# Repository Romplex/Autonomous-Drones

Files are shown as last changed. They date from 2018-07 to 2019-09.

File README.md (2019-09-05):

# Autonomous-Drones
## Pinout:
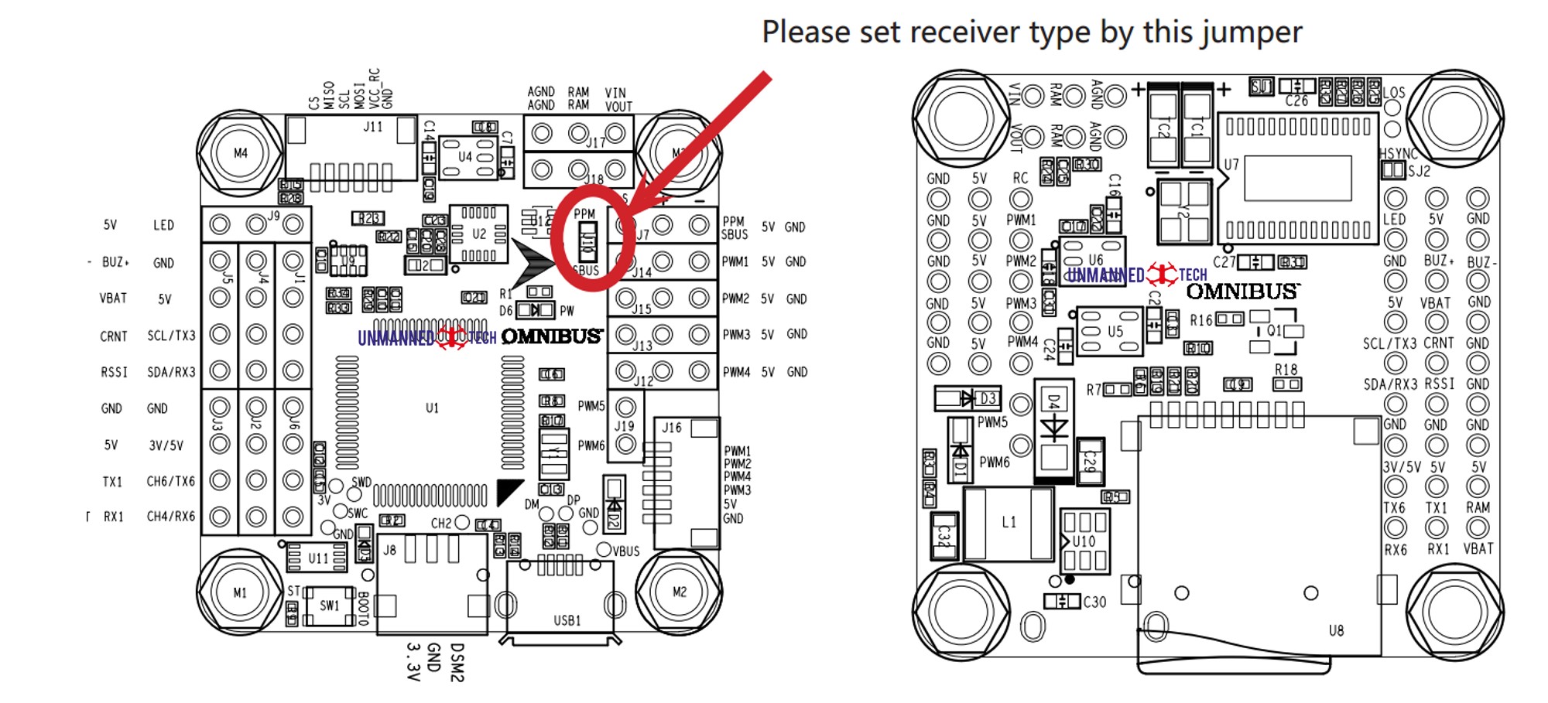
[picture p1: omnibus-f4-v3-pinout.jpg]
Omnibus Pinout


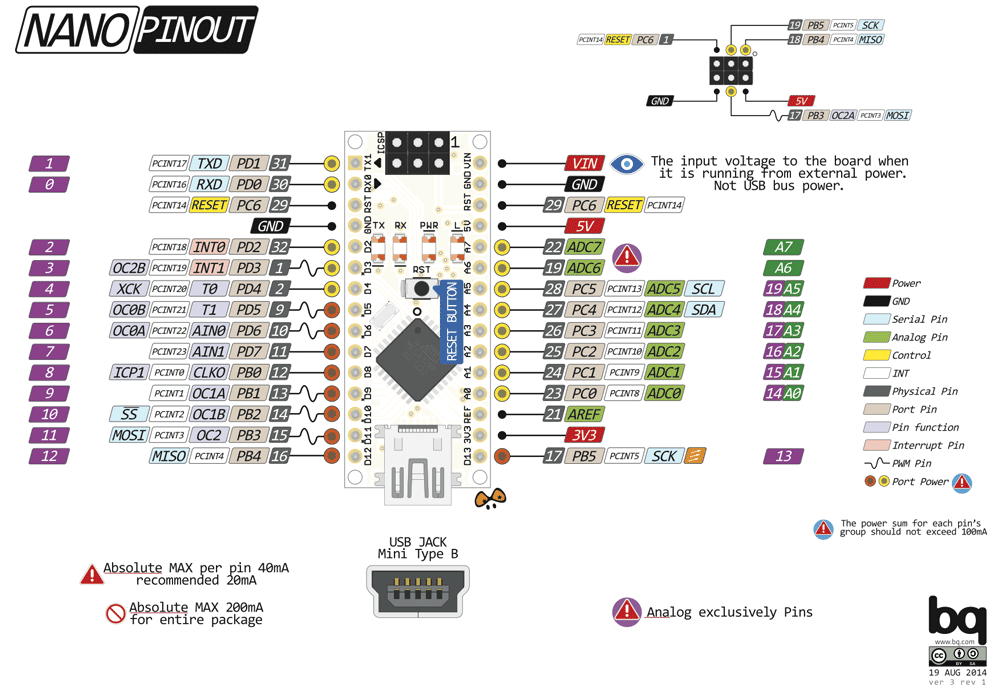
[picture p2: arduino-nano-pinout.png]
Arduino Nano Pinout


Pozyx Pinout

## Inav Settings:
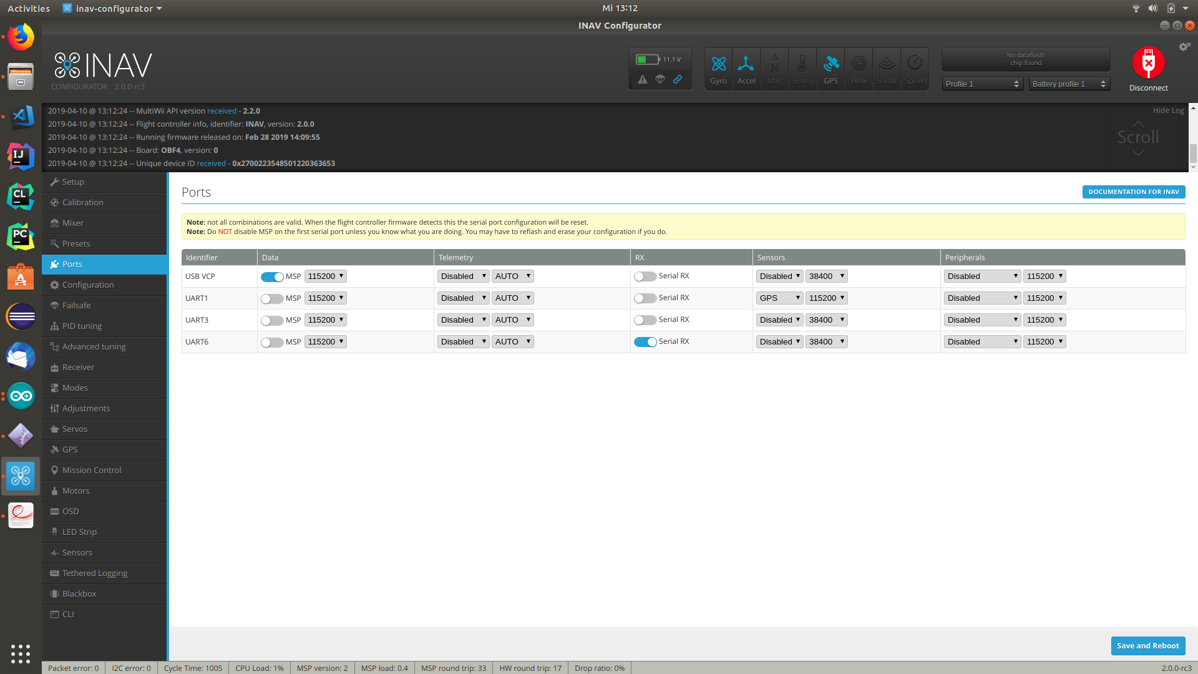
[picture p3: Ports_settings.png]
Inav Configurator Ports Inav ports


## Architektur für Kommunikation:
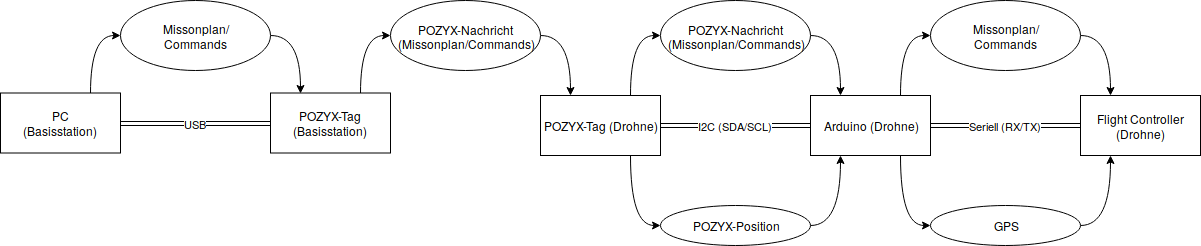
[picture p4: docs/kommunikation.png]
Logo Title Text 1


## LiPos Laden:
* Ladestärke 5A 
* 11.1V 
* LiPo (3S für 3 Zellen) 
* "Start" gedrükt halten bis es piept
* "Enter" zur Bestätigung der Einstellungen drücken

## POZYX Channel Settings
ultra-wideband channel 5, preamble length 1024, prf 64MHz, and bitrate 110kbps

## POZYX Anchor-IDs:
* 0x6951 - 1500mm
* 0x6e59 - 2000mm
* 0x695d - 2500mm
* 0x690b - 3000mm

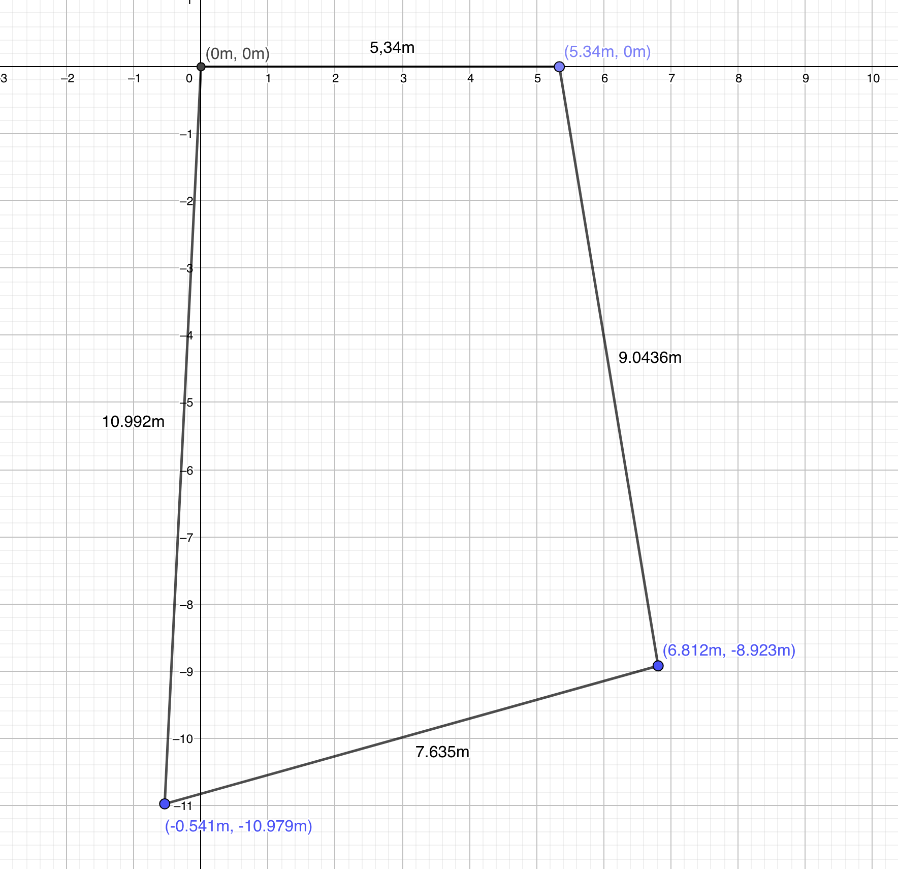
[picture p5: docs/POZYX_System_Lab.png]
Coords for anchors


## APROXIMATE GPS COORDINATES OF LAB
> 51.311644, 9.473625 (51°18'41.9"N 9°28'25.1"E)

## Useful Links:

[Ardupilot with Pozyx](http://ardupilot.org/copter/docs/common-pozyx.html)

[Drone not arming issues](https://github.com/iNavFlight/inav/wiki/%22Something%22-is-disabled----Reasons)

[iNAV GPS and COMPASS setup](https://github.com/iNavFlight/inav/wiki/GPS--and-Compass-setup)

[Omnibus F4 board infos](https://github.com/iNavFlight/inav/blob/master/docs/Board%20-%20Omnibus%20F4.md)

[Identify Omnibus F4 board](https://www.dronetrest.com/t/how-to-identify-what-omnibus-f4-board-you-have/4735)

## Info
* Arduino Nano Flash: old bootloader

## Verkabelung
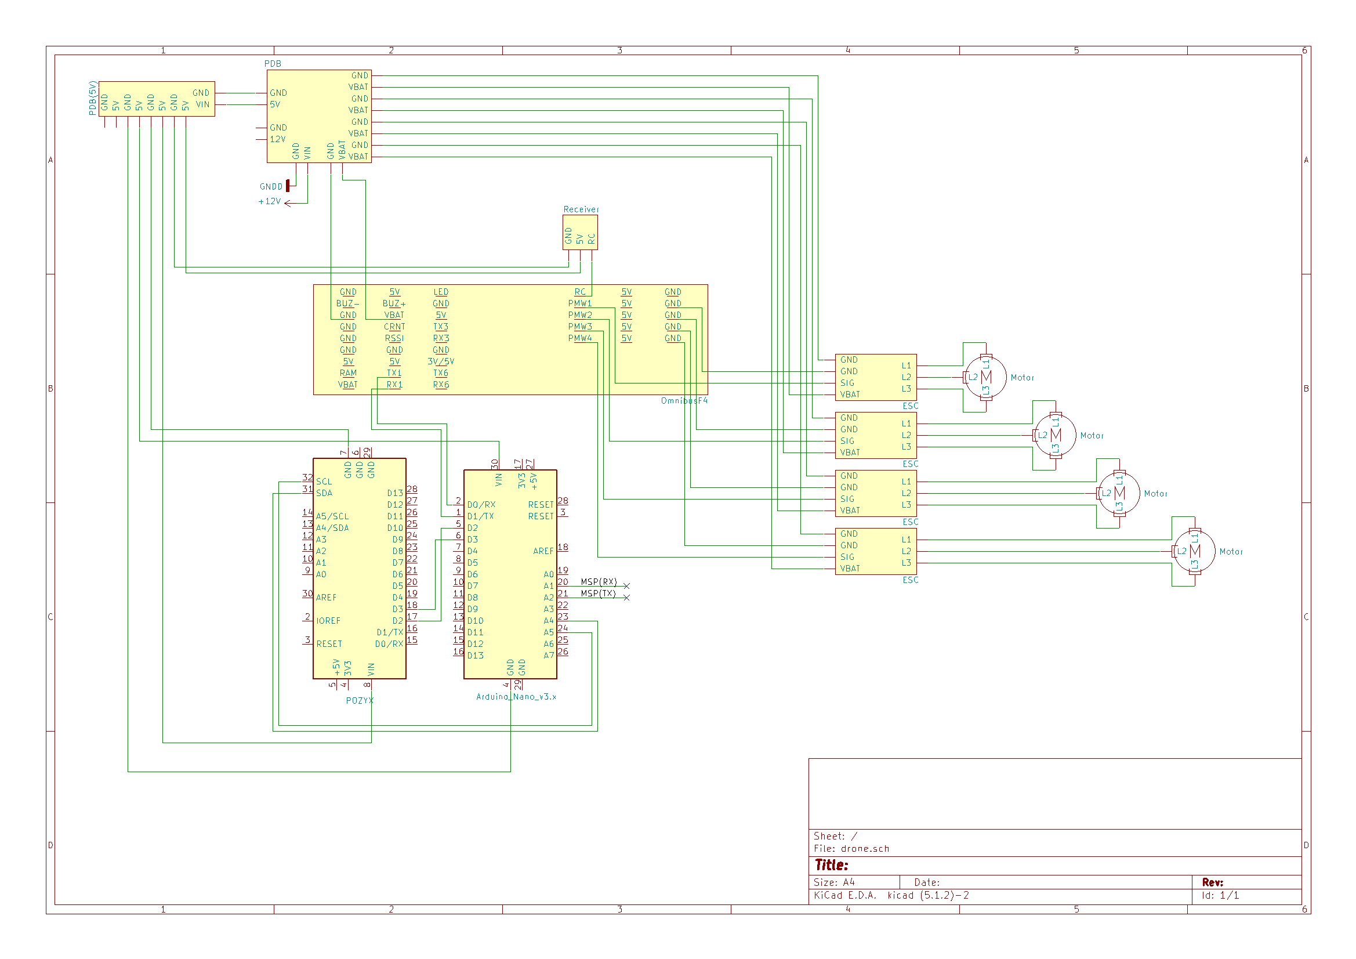
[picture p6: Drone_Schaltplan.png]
Drone Schaltplan

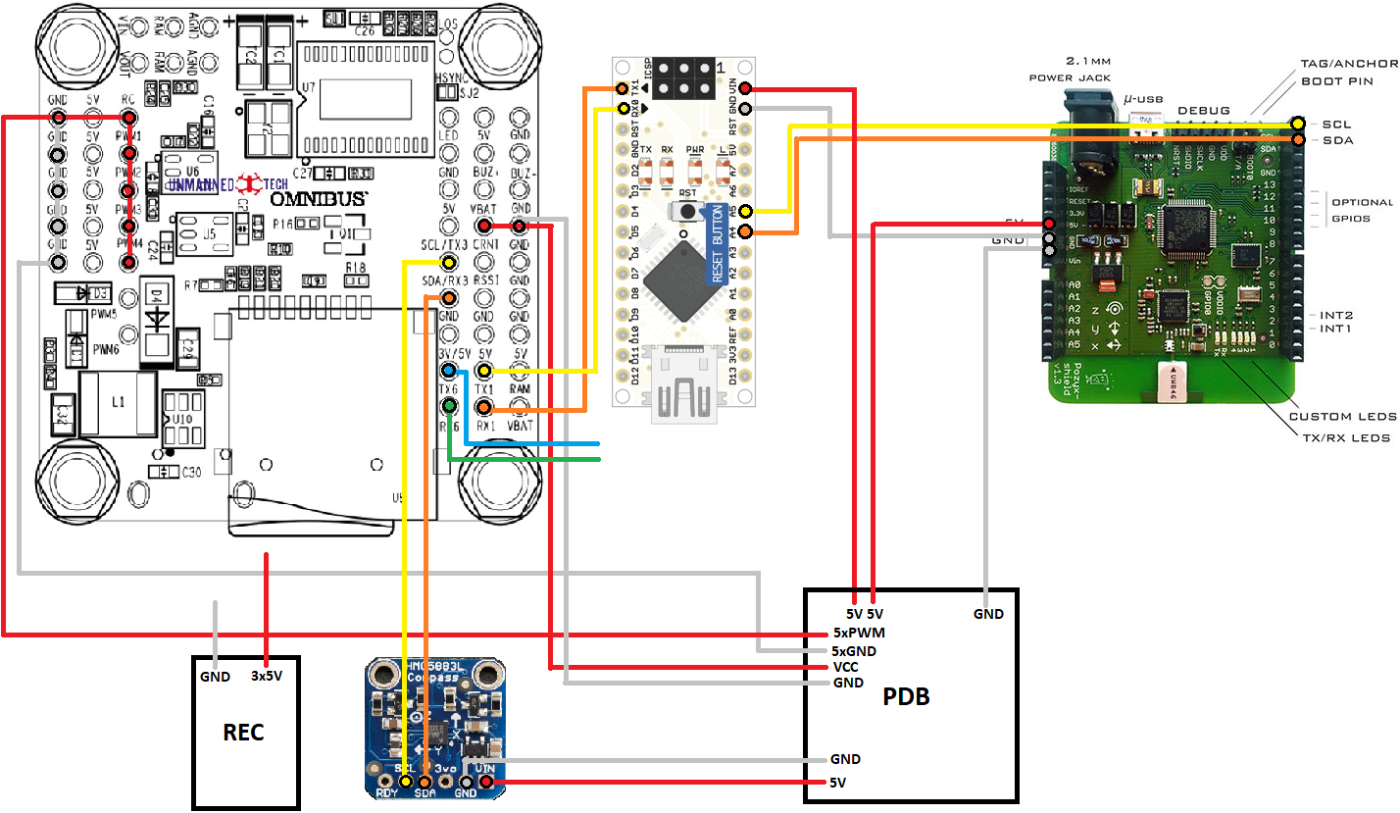
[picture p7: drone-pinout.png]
Drone Pinout


### POZYX -> Arduino Nano
* SDA -> SDA (Pin A4)
* SCL -> SCL (Pin A5)
* GND -> GND

### PDB -> POZYX 
* GND -> GND
* 5V -> 5V

### PDB -> FC
* 5Pin-PWM (Motoren) -> 5Pin-PWM
* 5Pin-GND -> 5Pin-GND
* VCC -> VBAT
* GND -> GND

### PDB -> Arduino Nano
* 5V -> Vin

### FC -> Arduino Nano
* RX1 -> TX1
* TX1 -> RX0

### FC -> REC
* 3Pin-GND -> GND
* 5V -> 3Pin-5V

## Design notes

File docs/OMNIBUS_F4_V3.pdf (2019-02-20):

1 4 . A U G U S T 2 0 1 7 | V O N | F L O R I

# OMNIBUS F4 V3 – Documentation

Since there is no documentation at all on any of these F4 boards, here is my try:
– STM32F405 LQFP64 (168Mhz, 1M ash, 192kB SRAM)
– MPU6000 6DOF IMU
– BMP280 barometer
– MAX7456 OSD (or fake)
– 5V Switching regulator (MP2359)
– 6pin SM06B-SRSS connector to ESC (ts Racestar RS20A4V2) – DSM2 port for SPEKTRUM satellit
– USB CDC serial, DFU rmware update
– micro SD card slot for Blackbox logging

Latest rmware on Betaight github releases (V3.2.0) Congurator as Chrome App

Specication:
Power Supply MP2359 (1.4MHz switching regulator)
Input Voltage: max 24V (input capacitors may limit voltage to 4S) Output Current: max. 1.2A (1.8A current Limit)

3.3V LDO (100mA?)

Accessable pins

LABEL PIN TIMER DMA LQFP64
PIN

NOTE

RSSI | A0 | | | 14 | Not ADC capable
PWM5 | A1 | 5,2 | 1,4 | 15 | SoftSer 11 RX(/TX)
PWM4 | A2 2,3 | 1,1 | 16 | Motor 4
PWM3 | A3 2,4 | 1,6 | 17 | Motor 3
PWM6 | A8 1,1 | 2,3 | 41 | SoftSer 11 TX(/RX)
UART1 TX | A9 1,2 | 2,2 | 42
UART1 RX | A10 1,3 | ?,? | 43 | DSM2 SPEKSAT
PWM1 | B0 3,3 | 1,7 | 26 | Motor 1
PWM2 | B1 | 3,4 | 1,2 | 27 | Motor 2
Buzzer | B4 | | | 56
LED_STRIP B6 4,1 | 1,0 | 58 | WS2812 LED
PPM | B8 12,3 | n.a | 61 | PPM (if jumpered)
CH2 | B9 | | | 62 | ? wrong in BF github.
UART3 TX B10 2,3(!) | ?,? | 29 | Shared I²C resource
UART3 RX B11 2,4(!) | ?,? | 30 | Shared I²C resource
CRNT | C1 | — | 2,4 | 9 | external current sense ADC
VBAT | C2 — | 2,4 | 10 | internal VBat voltage
| | | | | divider ADC

LABEL PIN TIMER DMA LQFP64 PIN

NOTE

UART6 TX C6 8,1 | 2,2 | 37
UART6 RX C7 8,2 | 2,3 | 38 | SBUS (if jumpered)

Note: Serial ports in CAPITALs are Serial1; Serial3; Serial6, Serial11 (=SoftSer1); Serial12 (=SoftSer2)
In sourcecode and portforwarding use number-1: serial0; serial2; serial5…

Internal

LABEL | PORT TIMER DMA LQFP64
PIN

NOTE

USB_D+ | A12 | 45 | USB data plus
USB_D- | A11 | 44 | USB data minus
SWD | A13 | 46 | SWD_DIO
SWC | A14 | 49 | SWD_CLK
OSC_IN | H0 | 5
OSC_OUT | H1 | 6
SPI1_MISO | A6 | 22 | MPU600 SPI
SPI1_MOSI | A7 | 23
SPI1_CLK | A5 | 21
SPI1_CS_MPU A4 | 20
MPU_INT | C4 | 24

MPU6000
Interrupt output
SPI2_MISO | B14 | 35 | SD card SPI
SPI2_MOSI | B15 | 36

LABEL | PORT TIMER DMA LQFP64
PIN

NOTE

SPI2_CLK | B13 | 34
SPI2_CS_SD | B12 | 33
SD_DETECT | B7 | 59 | SD Card detect switch
SPI3_MISO | C11 | 52 | BARO & OSD SPI
SPI3_MOSI | C12 | 53
SPI3_CLK | C10 | 51
SPI3_CS_Baro B3 | 55
SPI3_CS_OSD A15 | 50
INVERTER | C8 | 39 | Logic Level inverter enable
LED1 | C5 | 57 | onboard LED (blue)
| B2 | 28 | GND
| C3 | 11 | resistor with NRST?
| C13 | 2 | unrouted
| C14 | 3 | unrouted
| C15 | 4 | unrouted

Where to buy:
ebay (DE)
ebay (CN)

The following is pretty much for my own conguration, but might be useful for you as well:

Set throotle check min:
set min_check = 1045

Setup SoftSer 11 for runcam control: resource Motor 5 none
resource Motor 6 none
resource serial_rx 11 A1
resource serial_tx 11 A8

Get Mag working on UART3/I²C2: resource Serial_TX 3 none
resource Serial_RX 3 none
resource i2c_scl 2 b10
resource i2c_sda 2 b11

Dont forget to:
save

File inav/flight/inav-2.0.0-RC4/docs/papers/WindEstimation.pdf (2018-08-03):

IMU Wind Estimation (theory) | - 1 - | December 12, 2009

IMU Wind Estimation (Theory)

William Premerlani, 12/12/2009

Three dimensional wind vector can be estimated with a GPS receiver and the direction cosine matrix in an airframe that is flying with changes in attitude.
The starting point is the identity that relates the speed over ground to the airspeed and the wind:

wind speed vector in earth frame air speed vector in earth frame

speed over ground vector in earth frame

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
S V W

equation 1

Whenever the plane is changing attitude, it is possible to use a pair of GPS measurements and direction cosine matrix values to estimate the wind vector, assuming that the wind is about the same for both measurements. Two measurements about 1 second apart will do. The timing is not critical. Suppose we apply the previous equation to both sets of measurements, and take the sum and the difference of the equations. We will find the following two equations:
S2 − S1 = V2 − V1 | equation 2
( | )( | )
| 2
W | S2 + S1 − V2 + V1 = | equation 3

We can measure the 3 dimensional velocity over ground vectors with a GPS. If we can somehow compute the air speed vectors, we can compute the wind speed vector.
If the plane is pitching and/or turning, we can use equation 2 and the direction cosine matrix to estimate the airspeed.
We can make the approximation that for an airframe with a tail the air speed vector is parallel with the fuselage. (Actually, many of the following results hold even if that is not true.) In that case, the airspeed vector is equal to the magnitude of the airspeed, times the column of the direction cosine matrix that represents the fuselage. We assume that the majority of the change in speed vector over a one second time interval is due to a change in direction rather than a change in magnitude, so we assume a constant magnitude.

IMU Wind Estimation (theory) | - 2 - | December 12, 2009

That column of the direction cosine matrix will be rather accurate regarding the pitch of the plane, but there might be a yaw error. So, we represent the airspeed vector in terms of the fuselage column of the direction cosine matrix as follows:
() | ()
() | ()

column of the DCM that represents the fuselage residual yaw error in the direction cosine matrix

magnitude of the airspeed

0 | 0 | 1
sin | cos | 0
cos | sin | 0

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
θ | θ
θ | θ

V

V

equation 4

The following is obtained by substituting equation 4 into equation 2 and rearranging:
() | ()
() | () | ( | ) 2 | 1
0 | 0 | 1
sin | cos | 0
cos | sin | 0
S2 | S1 | ⋅ F − F

- −
− ≈ ⋅ | θ | θ
| θ | θ
V | equation 5

It is easy to show that equation 5 leads to the following equation for computing the airspeed:

F2 | F1
S2 | S1
−
− V ≈ | equation 6

By the way, equation 6 is valid even if the airspeed vector is not parallel to the fuselage, as long as they both rotate by approximately the same amount between the two measurements. Also note that the time between the measurements does not enter into the equation, and we have not taken the derivative of anything.
Equation 6 gives us a simple way to estimate airspeed without a pitot. All we have to do is to take the ratio of the magnitude of the change in GPS velocity divided by the magnitude of the change in the “fuselage” column of the direction cosine matrix. We could stop right here and still have a very useful result.
The next thing we need to do is to estimate any residual yaw error. First, we define unit vectors in the directions of the vectors in equation 5:
2 | 1
2 | 1
F F

F F f

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
equation 7

Equation 5 then becomes:
() | ()
() | ()

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
0 | 0 | 1
sin | cos | 0
cos | sin | 0
θ | θ
θ | θ
equation 8

IMU Wind Estimation (theory) | - 3 - | December 12, 2009

Actually, if we take a close look at equation 8, we realize that it can only be approximately satisfied, and that what we should have done in equation 4 was to use a more general representation for the attitude error in the DCM. But we can get an answer that is close enough for our purposes by solving the following equation for the yaw rotation residual error:
() | ()
() | () |
⋅
- − =

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
sin | cos
cos | sin
θ | θ
θ | θ
equation 9

Equation 9 is easy enough to solve for θ , it is equal to the angle between the projections on to the horizontal plane of the vectors in equation 2.
Substituting everything we know at this point back into equation 3, we arrive at the following equations for the estimates of the three components of the wind vector:
( ( )( | ) | ( ) ( | ))

2

1x | 2x | cos | 1x | 2x | sin | 1y | 2 y

x

S | S | V | F | F | F | F
W
+ | − ⋅ | ⋅ | + | − | ⋅ | + = | θ | θ
equation 10
( ( )( | ) | ( ) ( | ))

2

sin | cos 1y | 2 y | 1x | 2x | 1y | 2 y

y

S | S | V | F | F | F | F
W
+ | − ⋅ | ⋅ | + | + | ⋅ | + = | θ | θ
equation 11
( )
2
1z | 2z | 1z | 2z
z
S | S | V F | F W | + | − ⋅ | + = | equation 12

Equations 6, 9, 10, 11, and 12 define the method for estimating the wind velocity vector from a pair of GPS and IMU measurements. Implementation will be described in a separate report. The following observations can be made about the technique:
- It reports all 3 components of the wind vector. The Z component should be very useful for sailplane pilots.
- The method reports the wind in real time. Individual wind estimates can either be used for real time decisions and computations, or filtered to provide a more accurate estimate of the wind.
- For the method to work, the plane must change attitude. A simple test to determine whether it can be applied at any instant is whether or not the denominator of equation 6 exceeds a minimum threshold. It is not necessary for the plane to change its yaw angle for it to work, a change in pitch angle will do just as well.

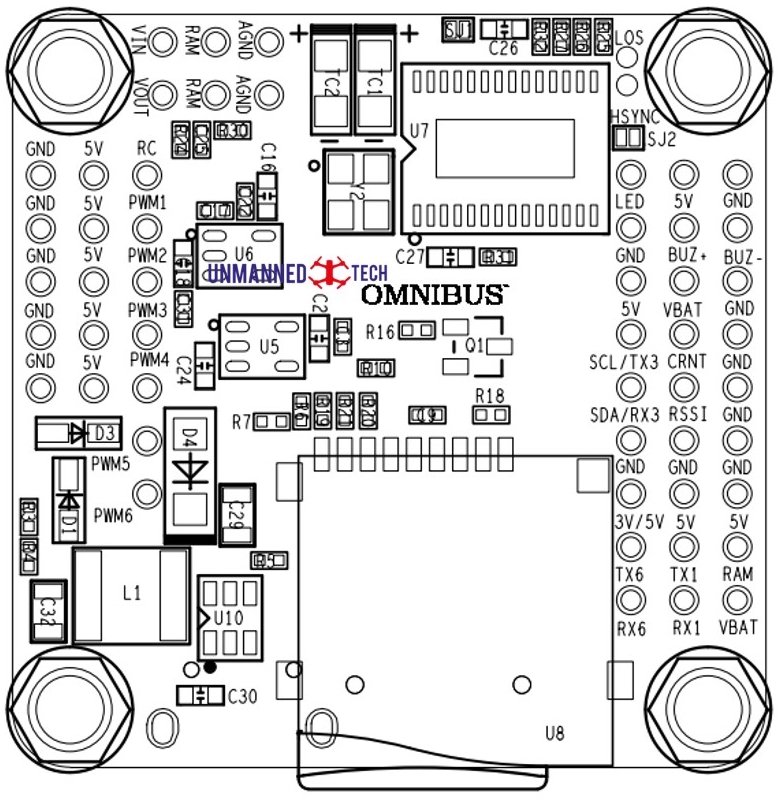
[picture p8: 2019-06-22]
omnibus-f4-v3-pinout-small.jpg

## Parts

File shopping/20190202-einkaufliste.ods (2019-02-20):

Beschreibung | Artikelbezeichnung | Stück | Stückpreis | Versand | gesammt | Lieferzeit | link
FC | Omnibus F4 v3 | 2 | 34.90 € | 0.00 € | 69.80 € | 1-3 Tage | https://www.graupner.de/Betaflight-Flight-Control-OMNIBUS-F4-V3-ICM20608-gyro/48374.ICMV3/
Bluetooth module | Aukru HC-06 | 2 | 7.99 € | 0.00 € | 15.98 € | 1-2 Tage | https://www.amazon.de/Aukru-Drahtlose-Bluetooth-Transceiver-Modul/dp/B00PL7SPGS
Magnetometer | HMC5883L | 2 | 5.15 € | 0.00 € | 10.30 € | 3-5 Tage | https://www.ebay.de/itm/GY-271-QMC5883-Kompass-Modul-3-Achsen-Magnetometer-Sensor-Arduino-HMC5883L/252881940433
Buchsenleisten gewinkelt 3 polig | - | 3 | 3.90 € | 2.70 € | 14.40 € | 7-8 Tage | https://www.ebay.de/itm/Buchsenleiste-90Grad-Stiftleiste-2-54-mm-3-x-30-pins-3-reihig-gewinkelt-90/292958572881
klett kabelbinder 100 stk | - | 1 | 8.97 € | 0.00 € | 8.97 € | 1-2 Tage | https://www.amazon.de/KEEPSORT®-Kabelbinder-Klettverschluss-Wiederverschließbare-Klett-Band-Kabelbinder-Schwarz/dp/B07BN8L5SX
Abstandshalter Schrauben 300 teilig | - | 1 | 11.69 € | 0.00 € | 11.69 € | 1-2 Tage | https://www.amazon.de/Rosenice-Abstandhalter-Schrauben-Muttern-schwarz/dp/B00W79JXFA
jumper kabel 3 x 40 x 20cm | - | 2 | 6.99 € | 0.00 € | 13.98 € | 1-2 Tage | https://www.amazon.de/Female-Female-Male-Female-Male-Male-Steckbrücken-Drahtbrücken-bunt/dp/B01EV70C78
 |  | 0 | 0.00 € | 0.00 € | 0.00 €
 |  | 0 | 0.00 € | 0.00 € | 0.00 €
 |  | 0 | 0.00 € | 0.00 € | 0.00 €
 |  | 0 | 0.00 € | 0.00 € | 0.00 €
 |  |  |  | SUMME: | 145.12 €

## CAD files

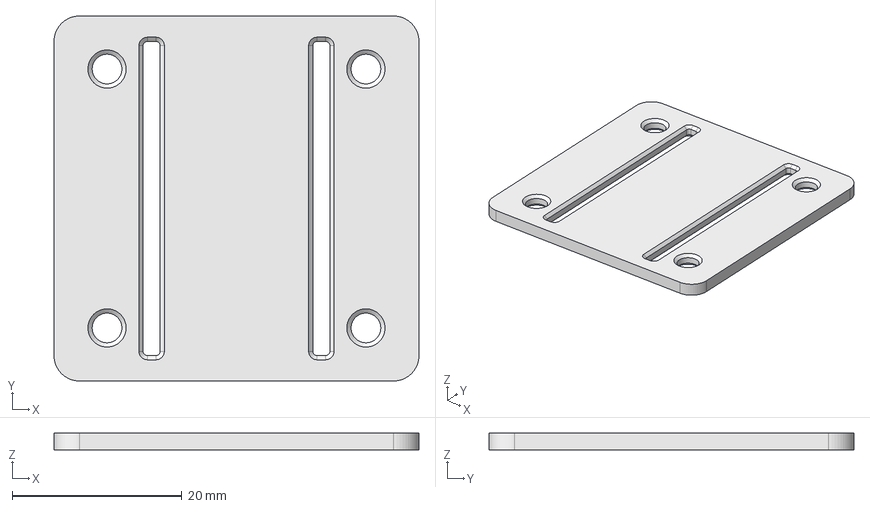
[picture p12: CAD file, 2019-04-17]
3dprints/plate_ardu_rec.FCStd
43.0 x 43.0 x 2.00 mm

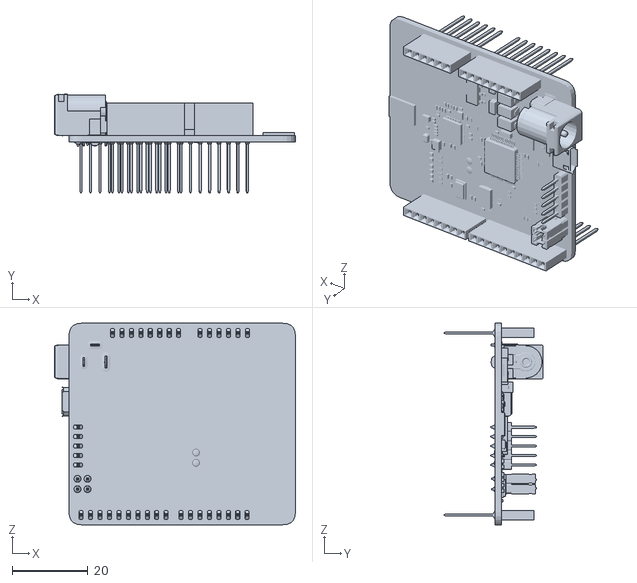
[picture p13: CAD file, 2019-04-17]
3dprints/dev_tag.obj
63.8 x 26.1 x 53.4

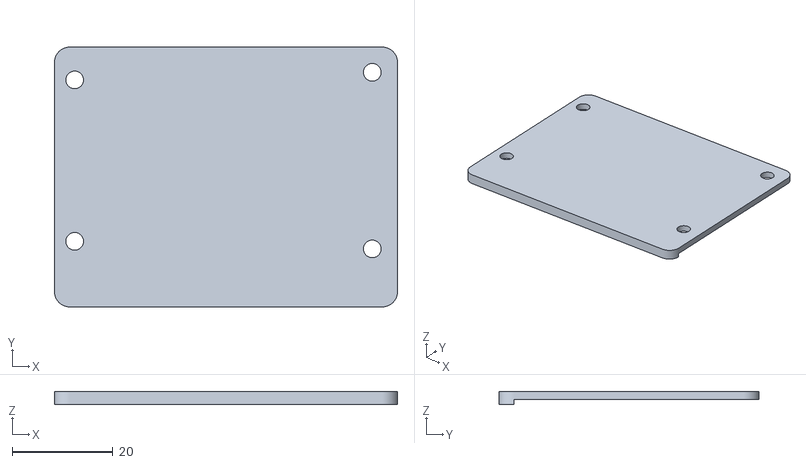
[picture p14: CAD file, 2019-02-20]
3dprints/pozyx_holder.stl
68.0 x 51.5 x 2.60

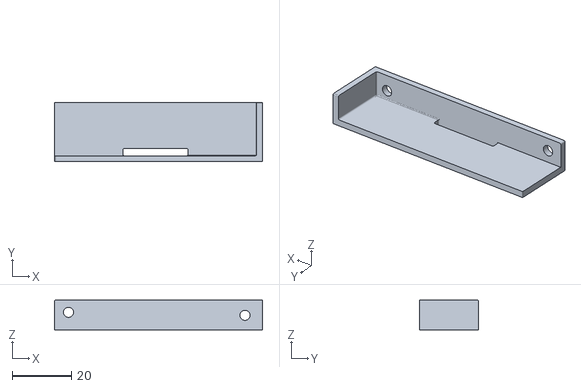
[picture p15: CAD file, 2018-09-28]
3dprints/bat_holder_v3.stl
70.0 x 20.0 x 10.0

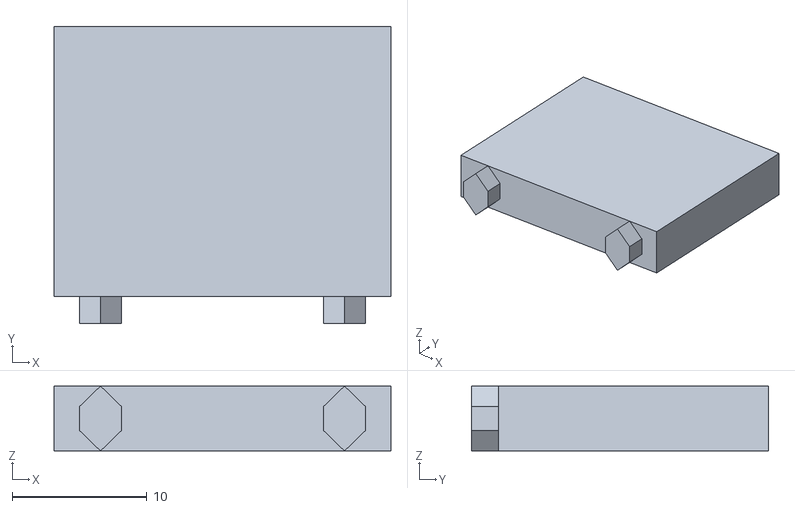
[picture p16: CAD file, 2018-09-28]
3dprints/bat_stop_v1.stl
25.0 x 22.0 x 4.81

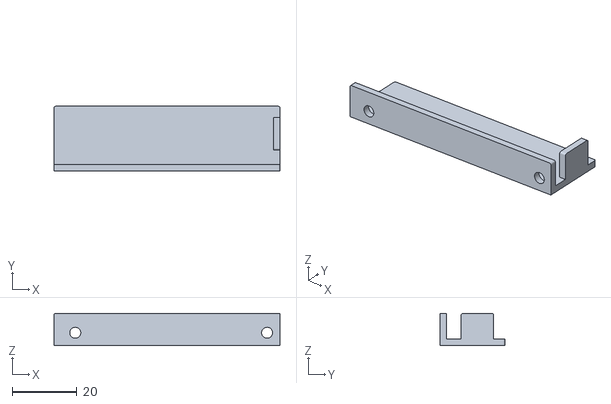
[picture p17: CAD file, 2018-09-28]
3dprints/bat_holder.stl
70.0 x 20.0 x 10.0

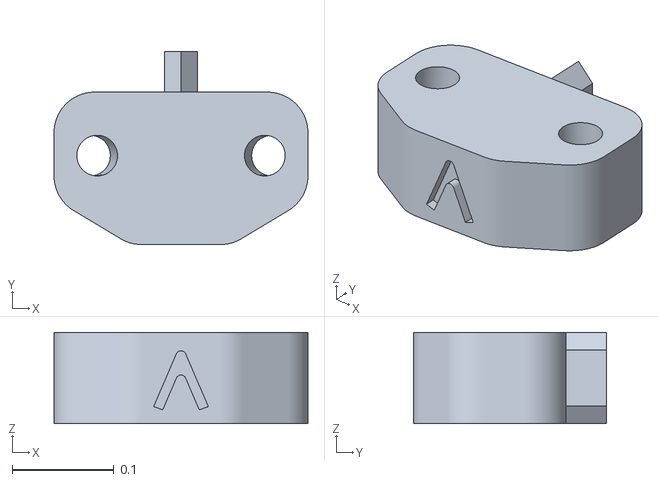
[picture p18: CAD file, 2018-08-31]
3dprints/new_foot_3.stl
0.25 x 0.19 x 0.09

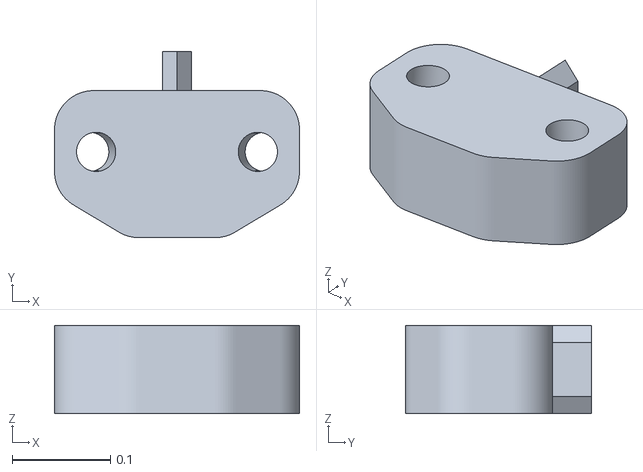
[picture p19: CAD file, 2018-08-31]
3dprints/new_foot_2.stl
0.25 x 0.19 x 0.09

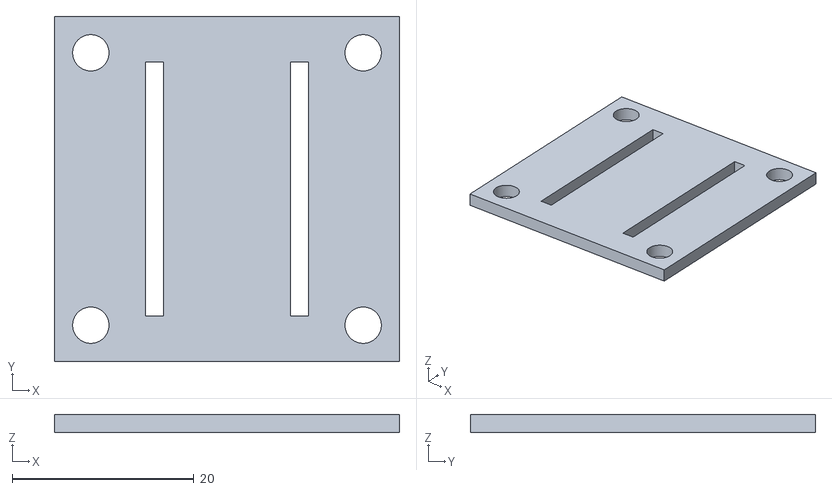
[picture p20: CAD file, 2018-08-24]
3dprints/receiver_base.stl
38.0 x 38.0 x 2.00

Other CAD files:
3dprints/base_ardu_rec.stl
3dprints/new_foot.stl
3dprints/bat_holder_v2.stl

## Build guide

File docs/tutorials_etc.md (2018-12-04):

# USEFUL INFO
##LiPos Laden:
# FIXME???!!!
Ladestaerke 5A -> 11.1V -> LiPo(3S fuer 3 Zellen) -> start gedruekt halten bis piept, dann enter zur Bestaetigung der Einstellungen

POZYX Anchor-IDs:
	0x6951 - 1500mm
	0x6e59 - 2000mm
	0x695d - 2500mm
	0x690b - 3000mm

# USEFUL LINKS

[Multiwii Serial Protocol (MSP) - Wiki](http://www.multiwii.com/wiki/index.php?title=Multiwii_Serial_Protocol)

[Ardupilot with Pozyx](http://ardupilot.org/copter/docs/common-pozyx.html)

[Drone not arming issues](https://github.com/iNavFlight/inav/wiki/%22Something%22-is-disabled----Reasons)

[iNAV GPS and COMPASS setup](https://github.com/iNavFlight/inav/wiki/GPS--and-Compass-setup)

[Identify Omnibus F4 board](https://www.dronetrest.com/t/how-to-identify-what-omnibus-f4-board-you-have/4735)

# APROXIMATE GPS COORDINATES OF LAB
##P1:	51.311644, 9.473625 (51��18'41.9"N 9��28'25.1"E)

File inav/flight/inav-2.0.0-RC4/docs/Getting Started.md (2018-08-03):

# Getting Started

This is a step-by-step guide that can help a person that has never used INAV before set up a flight controller and the aircraft around it for flight. Basic RC knowledge is required, though. A total beginner should first familiarize themselves with concepts and techniques of RC before using this (e.g. basic controls, soldering, transmitter operation etc). One could use [RCGroups](http://www.rcgroups.com/forums/index.php) and/or [the Youtube show FliteTest](https://www.youtube.com/user/flitetest) for this.

DISCLAIMER: This documents is a work in progress. We cannot guarantee the safety or success of your project. At this point the document is only meant to be a helping guide, not an authoritative checklist of everything you should do to be safe and successful. Always exercise common sense, critical thinking and caution.

Read the [Introduction](Introduction.md) chapter for an overview of INAV and how the community works.

## Hardware

NOTE: Flight Controllers are typically equipped with accelerometers. These devices are sensitive to shocks. When the device is not yet installed  to an aircraft, it has very little mass by itself. If you drop or bump the controller, a big force will be applied on its accelerometers, which could potentially damage them. Bottom line: Handle the board very carefully until it's installed on an aircraft!

For an overview of the hardware INAV (hereby CF) can run on, see [Boards.md](Boards.md). For information about specific boards, see the board specific documentation.

* Assuming that you have a flight controller board (hereby FC) in hand, you should first read through the manual that it came with. You can skip the details about software setup, as we'll cover that here.

* Decide how you'll connect your receiver by reading the [receiver](Rx.md) chapter, and how many pins you need on the outputs (to connect ESCs and servos) by reading about [Mixers](Mixer.md).

* If you're interested in monitoring your flight battery with CF, see [Battery Monitoring](Battery.md).

* You may want audible feedback from your copter so skim through [Buzzer](Buzzer.md) and mark the pins that will be used.

* Do you want your RC Receiver's RSSI to be sent to the board? [The RSSI chapter](Rssi.md) explains how. You may or may not need to make an additional connection from your Receiver to the FC.

* Would you like to try using a GPS unit to get your aircraft to Loiter or Return-To-Launch? Take a look at the [GPS](Gps.md) and [GPS Tested Hardware](Gps.md#hardware) chapters.

* You may also want to read the [Serial](Serial.md) chapter to determine what extra devices (such as Blackbox, OSD, Telemetry) you may want to use, and how they should be connected.

* Now that you know what features you are going to use, and which pins you need, you can go ahead and solder them to your board, if they are not soldered already. Soldering only the pins required for the application may save weight and contribute to a neater looking setup, but if you need to use a new feature later you may have to unmount the board from the craft and solder missing pins, so plan accordingly.  Before soldering your FC please review a how-to-solder tutorial to avoid expensive mistakes, practice soldering on some scrap before soldering your FC.

* If you are going to use [Oneshot125](Oneshot.md), you may need to enable that on your ESCs using a jumper or flashing them with the latest stable firmware and enable Damped Light in their settings, if it's supported. Refer to the ESCs' documentation or online discussions to determine this.

## Software setup

Now that your board has pins on it, you are ready to connect it to your PC and flash it with CF. Install the Chromium browser or Google Chrome to your PC, if you don't have it already, add the [INAV Configurator](https://chrome.google.com/webstore/detail/inav-configurator/fmaidjmgkdkpafmbnmigkpdnpdhopgel) to it, and start it.

Then follow these instructions for [Installation](Installation.md) of the firmware to the FC.

## INAV Configuration

Your FC should now be running CF, and you should be able to connect to it using the Configurator. If that is not the case, please go back to the previous sections and follow the steps carefully.

<!--- This next paragraph should probably contain less info, as this info already exists in Configuration.md -->
Now, there are two ways to [configure CF](Configuration.md); via  the Configurator's tabs (in a "graphical" way, clicking through and selecting/changing values and tickboxes) and using the [Command Line Interface (CLI)](Cli.md). Some settings may only be configurable using the CLI and some settings are best configured using the GUI (particularly the ports settings, which aren't documented for the CLI as they're not human friendly).

* It is now a good time to setup your RC Receiver and Transmitter. Set the Tx so that it outputs at least 4 channels (Aileron, Elevator, Throttle, Rudder) but preferably more. E.g. you can set channels 5 and 6 to be controlled by 3-position switches, to be used later. Maybe set up EXPO on AIL/ELE/RUD, but you should know that it can also be done in CF's software later. If using RSSI over PPM or PWM, it's now time to configure your Rx to output it on a spare channel.

* Connect the Rx to the FC, and the FC to the PC. You may need to power the Rx through a BEC (its 5V rail - observe polarity!).

* On your PC, connect to the Configurator, and go to the first tab. Check that the board animation is moving properly when you move the actual board. Do an accelerometer calibration.

* Configuration tab: Select your aircraft configuration (e.g. Quad X), and go through each option in the tab to check if relevant for you.

  * E.g. you may want to enable ONESHOT125 for Oneshot-capable ESCs.
  * You may need RX_PPM if you're using an RC Receiver with PPM output etc.
  * If planning to use the battery measurement feature of the FC, check VBAT under Battery Voltage.
  * If using analog RSSI, enable that under RSSI. Do not enable this setting if using RSSI injected into the PPM stream.
  * Motors will spin by default when the FC is armed. If you don't like this, enable MOTOR_STOP.
  * Also, adjust the minimum, middle and maximum throttle according to these guidelines:

    * Minimum Throttle - Set this to the minimum throttle level that enables all motors to start reliably. If this is too low, some motors may not start properly after spindowns, which can cause loss of stability and control. A typical value would be 1100.
    * Middle Throttle - The throttle level for middle stick position. Many radios use 1500, but some (e.g. Futaba) may use 1520 or other values.
    * Maximum Throttle - The maximum throttle level that the ESCs should receive. A typical value would be 2000.
    * Minimum Command - This is the "idle" signal level that will be sent to the ESCs when the craft is disarmed, which should not cause the motors to spin. A typical value would be 1000.
  * Finally, click Save and Reboot.

* Receiver tab:
    * Check that the channel inputs move according to your Tx inputs.
    * Check that the Channel map is correct along with the RSSI Channel, if you use that.
    * Verify the range of each channel goes from ~1000 to ~2000.  See also [controls](Controls.md). and `rx_min_usec` and `rx_max_usec`.
    * You can also set EXPO here instead of your Tx.
    * Click Save!
* Modes tab: Setup the desired modes. See the [modes](Modes.md) chapter for what each mode does, but for the beginning you mainly need HORIZON, if any.

* Before finishing this section, you should calibrate the ESCs, install the FC to the frame, and connect the RSSI cable, buzzer and battery if you have chosen to use those.

## Final testing and safety

It's important that you have configured CF properly, so that your aircraft does not fly away, or even worse fly into property and people! This is an important step that you should NOT postpone until after your maiden flight. Please do this now, before you head off to the flying field.

* First, learn how to arm your FC, and about other [controls](Controls.md).
* Next up, setup [Failsafe](Failsafe.md). Take your time, do it properly.
* Now, on the bench, without props, test that failsafe works properly, according to the above doc.
* Additionally, test the effect of AIL/ELE input of your Tx. Is the aircraft responding properly? Do the same for RUD input.
* Test the direction of AIL/ELE auto correction. Raise throttle at 30% (no blades!); when you tilt the aircraft, do the motors try to compensate momentarily? This should simulate random wind forces that the FC should counteract
* Test the direction of AIL/ELE auto correction in HORIZON mode. With throttle at 30%, if you tilt the aircraft so that one motor is lowered towards the ground, does it spin up and stay at high RPM until you level it off again? This tests the auto-leveling direction.

If one of these tests fail, do not attempt to fly, but go back to the configuration phase instead. Some channel may need reversing, or the direction of the board is wrong.

## Using it (AKA: Flying)

Go to the field, turn Tx on, place aircraft on the ground, connect flight battery and wait. Arm and fly. Good luck!

## Advanced Matters

Some advanced configurations and features are documented in the following pages, but have not been touched-upon earlier:

* [Profiles](Profiles.md)
* [PID tuning](PID%20tuning.md)
* [In-flight Adjustments](Inflight%20Adjustments.md)
* [Blackbox logging](Blackbox.md)
* [Using a Sonar](Sonar.md)
* [Spektrum Bind](Spektrum%20bind.md)
* [Telemetry](Telemetry.md)
* [Using a Display](Display.md)
* [Using a LED strip](LedStrip.md)

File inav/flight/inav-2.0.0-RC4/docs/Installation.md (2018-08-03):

# Installation

## Using the configurator
This is a generic procedure to flash a board using the configurator. The configurator does not yet support all boards, so please check the documentation corresponding to your board before proceeding.

Make sure you have the [INAV Configurator](https://github.com/iNavFlight/inav-configurator) installed, then:

* Connect the flight controller to the PC.
* Start the INAV Configurator.
* Click on "Disconnect" if the configurator connected to the board automatically.
* Click on the "Firmware Flasher" tab.
* Make sure you have internet connectivity and click on the "Load Firmware [Online]" button.
* Click on the "Choose a Firmware / Board" dropdown menu, and select the latest stable version for your flight controller.
* IMPORTANT: Read and understand the release notes that are displayed.  When upgrading review all release notes since your current firmware.
* If this is the first time INAV is flashed to the board, tick the "Full Chip Erase" checkbox.
* Connect the flight controller board to the PC.  Ensure the correct serial port is selected.
* Click on the "Flash Firmware" button and hold still (do not breathe, too).
* When the progress bar becomes green and reads "Programming: SUCCESSFUL" you are done!

## Manually

See the board specific flashing instructions.

# Upgrading

When upgrading be sure to backup / dump your existing settings.  Some firmware releases are not backwards compatible and default settings are restored when the FC detects an out of date configuration.

## Backup/Restore process

See the CLI section of the docs for details on how to backup and restore your configuration via the CLI.

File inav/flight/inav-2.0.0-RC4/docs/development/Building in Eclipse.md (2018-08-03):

# Short Version
Install the latest Eclipse Standard/SDK and install the **C/C++ developments Tools** plugins
plugin eclipse

Import the project using the wizard **Existing Code as Makefile Project**


Adjust your build option if necessary


Make sure you have a valid ARM toolchain and Ruby in the path


# Long version
* First you need an ARM toolchain. Good choices are **GCC ARM Embedded** (https://launchpad.net/gcc-arm-embedded) or **Yagarto** (http://www.yagarto.de).
* Install Ruby (see the document for your operating system).
* Now download Eclipse and unpack it somewhere. At the time of writing Eclipse 4.2 was the latest stable version.
* To work with ARM projects in Eclipse you need a few plugins:
	+ **Eclipse C Development Tools** (CDT) (available via *Help > Install new Software*).
	+ **Zylin Embedded CDT Plugin** (http://opensource.zylin.com/embeddedcdt.html).
	+ **GNU ARM Eclipse** (http://sourceforge.net/projects/gnuarmeclipse/).
	+ If you want to hook up an SWD debugger you also need the **GDB Hardware Debugging** plugin (Also available via *Install new Software*).
* Now clone the project to your harddrive.
* Create a new C project in Eclipse and choose ARM Cross Target Application and your ARM toolchain.
* Import the Git project into the C project in Eclipse via *File > Import > General > File System*.
* Activate Git via *Project > Team > Share Project*.
* Switch to the development branch in Eclipse (*Project > Team > Switch To > development*).
* The next thing you need to do is adjust the project configuration. There is a Makefile included that works but you might want to use GNU ARM Eclipse's automatic Makefile generation. Open the Project configuration and go to *C/C++ Build > Settings*
	* Under *Target Processor* choose "cortex-m3"
	* Under *ARM Yagarto [Windows/Mac OS] Linker > General* (or whatever toolchain you chose)
		+ Browse to the Script file *stm32_flash.ld*
		+ Uncheck "Do not use standard start files"
		+ Check "Remove unused sections"	
	* Under *ARM Yagarto [Windows/Mac OS] Linker > Libraries*
		+ Add "m" for the math library
	* Under *ARM Yagarto [Windows/Mac OS] Compiler > Preprocessor* add the following 2 items to "Defined Symbols":
		+ STM32F10X_MD
		+ USE_STDPERIPH_DRIVER
	* Under *ARM Yagarto [Windows/Mac OS] Compiler > Directories* add the following 3 items
		+ ${workspace_loc:/${ProjName}/lib/CMSIS/CM3/CoreSupport}
		+ ${workspace_loc:/${ProjName}/lib/CMSIS/CM3/DeviceSupport/ST/STM32F10x}
		+ ${workspace_loc:/${ProjName}/lib/STM32F10x_StdPeriph_Driver/inc}
	* Under *ARM Yagarto [Windows/Mac OS] Compiler > Miscellaneous* add the following item to "Other flags":
		+ -fomit-frame-pointer
* The code in the support directory is for uploading firmware to the board and is meant for your host machine. Hence, it must not be included in the build process. Just right-click on it to open its properties and choose "Exclude from build" under *C/C++ Build > Settings*
* The last thing you need to do is adding your toolchain to the PATH environment variable.
	+ Go to *Project > Properties > C/C++ Build > Environment*, add a variable named "PATH" and fill in the full path of your toolchain's binaries.
	+ Make sure "Append variables to native environment" is selected.		   
* Try to build the project via *Project > Build Project*.
* **Note**: If you're getting "...could not be resolved" errors for data types like int32_t etc. try to disable and re-enable the Indexer under *Project > Properties > C/C++ General > Indexer*.

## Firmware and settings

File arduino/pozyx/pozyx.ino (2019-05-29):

#include <Pozyx.h>
#include <Pozyx_definitions.h>
#include <Wire.h>
#include <SoftwareSerial.h>

#define FILTER_TYPE_NONE            0x0
#define FILTER_TYPE_FIR             0x1
#define FILTER_TYPE_MOVING_AVERAGE  0x3
#define FILTER_TYPE_MOVING_MEDIAN   0x4

#define ID_NAV "POS"          // message ID for location data
#define ID_MAG "DIR"          // message ID for course data

/******************
     Pozyx data
*******************/
// TODO check if all data has correct units for fc navigation
typedef struct __attribute__((packed))_pozyx_data {
  magnetic_t magnetic;
  coordinates_t linear_velocity;        // cm/s
  unsigned long last_time;              // ms
  coordinates_t coordinates;            // mm
  uint16_t source_id;                   // the network id of the connected device, will be set automatically
  //pos_error_t pos_error;                // x|y|z variance and xy|xz|yz covariance
} pozyx_data_t;

volatile pozyx_data_t pozyx_data;
bool newOrientation = false;
bool newPosition = false;

//#define DEBUG
#define USE_POZYX
#define PRINT_POSITION
#define PRINT_ORIENTATION

#ifndef USE_POZYX
pozyx_data.coordinates.x = pozyx_data.coordinates.y = 0;  // mm
pozyx_data.coordinates.z = 0;                             // mm

//pozyx_data.angular_vel.x = pozyx_data.angular_vel.y = pozyx_data.angular_vel.z = 0; // degrees per second
pozyx_data.magnetic.x = pozyx_data.magnetic.y = pozyx_data.magnetic.z = 0;  // µT
#endif

SoftwareSerial msp(A1, A2); // rx/tx

unsigned long t_gps;
unsigned long t_mag;

String inputString = "";            // a string to hold incoming data
boolean stringComplete = false;     // whether the string is complete

// FILTER_TYPE_NONE | FILTER_TYPE_MOVING_AVERAGE | FILTER_TYPE_MOVING_MEDIAN |
// FILTER_TYPE_:
//  NONE (Default value). No additional filtering is applied.
//  FIR. A low-pass filter is applied which filters out high-frequency jitters.
//  MOVING_AVERAGE. A moving average filter is applied, which smoothens the trajectory.
//  MOVING_MEDIAN. A moving median filter is applied, which filters out outliers

//        #############################################
//        ######### APPLY TAG PARAMETERS HERE #########
//        #############################################

// TODO compass should be updated at 10hz ?
// TODO gps should be updated at 18hz?
const unsigned int GPS_INTERVAL = 1;      // every 250ms
const unsigned int MAG_INTERVAL = 1;     // every  30ms

const uint8_t filter = FILTER_TYPE_MOVING_MEDIAN;
const uint8_t filter_strength = 8;  // 0-15

const uint8_t num_anchors = 5;                                      // the number of anchors
uint16_t anchors[num_anchors] = {0x6951, 0x6E59, 0x695D, 0x690B, 0x6748};   // network ids of the anchors
int32_t anchors_x[num_anchors] = {0, 5340, 6812, -541, 6812};            // anchor x-coorindates in mm
int32_t anchors_y[num_anchors] = {0, 0, -8923, -10979, -4581};            // anchor y-coordinates in mm
int32_t heights[num_anchors] = {1500, 2000, 2500, 3000, 200};           // anchor z-coordinates in mm


// UWB settings:
//    FAST(100ms bootup required): 110kbps, preamble length 1024 -> 51Hz
//    PRECISION:                   110kbps, preamble length 1024 -> 18Hz

uint8_t algorithm = POZYX_POS_ALG_TRACKING;             // try POZYX_POS_ALG_TRACKING for fast moving objects. (POZYX_POS_ALG_TRACKING|POZYX_POS_ALG_UWB_ONLY)
uint8_t dimension = POZYX_3D;                           // positioning dimension
int32_t height = 1000;

//        #############################################
//        ######### APPLY TAG PARAMETERS HERE #########
//        #############################################


void setup() {
  Serial.begin(115200); // 115200 mag and gps baudrate
  msp.begin(9600);      // 9600 softserial baudrate for msp
  while (!Serial);
  while (!msp);

  // setup time variables for gps and mag messages
  t_gps = 0;
  t_mag = 0;

  pozyx_data.last_time = 0;

#ifdef USE_POZYX

#ifdef DEBUG
  Serial.println("-   INIT POZYX   -");
#endif

  // possible interrupts (do bit-wise combinations):
  //    POZYX_INT_MASK_ERR, POZYX_INT_MASK_POS, POZYX_INT_MASK_IMU, POZYX_INT_MASK_RX_DATA, POZYX_INT_MASK_FUNC.
  //    POZYX_INT_MASK_ALL to trigger on all events.
  while (Pozyx.begin(false, MODE_INTERRUPT, POZYX_INT_MASK_ALL, 0) == POZYX_FAILURE) {

#ifdef DEBUG
    Serial.println("ERROR: Unable to connect to POZYX shield");
    Serial.flush();
#endif
    delay(1000);
  }

#endif

#ifdef USE_POZYX
  // read the network id of this device
  Pozyx.regRead(POZYX_NETWORK_ID, (uint8_t*)&pozyx_data.source_id, 2);

#ifdef DEBUG
  Serial.print("Source ID: "); Serial.println(pozyx_data.source_id, HEX);
#endif

  // clear all previous devices in the device list
  Pozyx.clearDevices(pozyx_data.source_id);
  // sets the anchor manually
  setAnchorsManual();

  // sets the positioning algorithm
  Pozyx.setPositionAlgorithm(algorithm, dimension, pozyx_data.source_id);

  // apply positioning filter and strength
  Pozyx.setPositionFilter(filter, filter_strength);

  // set update intervall for continuous mode
  // TODO is doPositioning still needed?
  Pozyx.setUpdateInterval(101); //100ms-60000ms
#endif

#ifdef DEBUG
  Serial.println(F("Starting positioning: "));
#endif
  Serial.flush();
#ifdef USE_POZYX
  delay(1500);
#endif

}

void loop() {

  unsigned long currentTime = millis();
  int status = 0;


#ifdef USE_POZYX
  // possible status flags:
  //    POZYX_INT_STATUS_ERR, POZYX_INT_STATUS_POS, POZYX_INT_STATUS_IMU,
  //    POZYX_INT_STATUS_RX_DATA, POZYX_INT_STATUS_FUNC

  /*if(Pozyx.waitForFlag(POZYX_INT_STATUS_ERR, 1)) {
    printErrorCode("");
    }*/

  if (Pozyx.waitForFlag(POZYX_INT_STATUS_IMU, 1)) {
    // update new magnetic and vel data
    Pozyx.getMagnetic_uT(&pozyx_data.magnetic);
    linear_acceleration_t accel;
    Pozyx.getLinearAcceleration_mg(&accel);

    if (pozyx_data.last_time != 0) {
      // calculate linear velocity
      unsigned long delta_t = currentTime - pozyx_data.last_time;

      pozyx_data.linear_velocity.x = accel.x * delta_t / 10; // cm/s
      pozyx_data.linear_velocity.y = accel.y * delta_t / 10; // cm/s
      pozyx_data.linear_velocity.z = accel.z * delta_t / 10; // cm/s
    }
    pozyx_data.last_time = currentTime;

    newOrientation = true;

  }

  if (Pozyx.waitForFlag(POZYX_INT_STATUS_POS, 2)) {
    Pozyx.getCoordinates(&pozyx_data.coordinates);
    //    Pozyx.getPositionError(&pozyx_data.pos_error);
    // TODO caluclate dilution of precision from pos error
    newPosition = true;
  }

  /*if (Pozyx.waitForFlag(POZYX_INT_STATUS_RX_DATA, 1))
    // we have received a message via pozyx
    forwardMsgToFC();*/
#endif

  if (currentTime - t_gps >= GPS_INTERVAL && newPosition) {
    // time to send position
    forwardNavigation(millis());
    newPosition = false;
  }

  if (currentTime - t_mag >= MAG_INTERVAL && newOrientation) {
    // time to send orientation
    forwardOrientation(millis());
    newOrientation = false;
  }

  while (msp.available()) {
    // get msp msg from fc
    char inChar = (char)msp.read();

    // TODO check when msp message ends (probably not '\n')
    if (inChar == '\n') {
      stringComplete = true;
    } else {
      inputString += inChar;
    }

#ifdef DEBUG
    Serial.print("incoming msp msg: "); Serial.println(inputString);
#endif
  }

  if (stringComplete) {
    forwardMsgToPOZYX();
  }
}

// error printing function for debugging
void printErrorCode(String operation) {
  uint8_t error_code;
  if (pozyx_data.source_id == NULL) {
    Pozyx.getErrorCode(&error_code);
    Serial.print("ERROR ");
    Serial.print(operation);
    Serial.print(", local error code: 0x");
    Serial.println(error_code, HEX);
    return;
  }
  int status = Pozyx.getErrorCode(&error_code, pozyx_data.source_id);
  if (status == POZYX_SUCCESS) {
    Serial.print("ERROR ");
    Serial.print(operation);
    Serial.print(" on ID 0x");
    Serial.print(pozyx_data.source_id, HEX);
    Serial.print(", error code: 0x");
    Serial.println(error_code, HEX);
  } else {
    Pozyx.getErrorCode(&error_code);
    Serial.print("ERROR ");
    Serial.print(operation);
    Serial.print(", couldn't retrieve remote error code, local error: 0x");
    Serial.println(error_code, HEX);
  }
}

// function to manually set the anchor coordinates
void setAnchorsManual() {
  for (int i = 0; i < num_anchors; i++) {
    device_coordinates_t anchor;
    anchor.network_id = anchors[i];
    anchor.flag = 0x1;
    anchor.pos.x = anchors_x[i];
    anchor.pos.y = anchors_y[i];
    anchor.pos.z = heights[i];
    Pozyx.addDevice(anchor, pozyx_data.source_id);
  }
  if (num_anchors > 4) {
    Pozyx.setSelectionOfAnchors(POZYX_ANCHOR_SEL_AUTO, num_anchors, pozyx_data.source_id);
  }
}

// format time: hhmmss.sss
String formatTime(unsigned long t) {
  int dd = t / 86400000;
  int hh = (t % 86400000) / 3600000;
  int mm = ((t % 86400000) % 3600000) / 60000;
  double ss = (((t % 86400000) % 3600000) % 60000) / 1000.0;

  String h = (hh > 9 ? String(hh) : "0" + String(hh));
  String m = (mm > 9 ? String(mm) : "0" + String(mm));
  String s = (ss > 9 ? String(ss, 3) : "0" + String(ss, 3));
  return h + m + s;
}

// NMEA CRC: XOR each byte with previous for all chars between '$' and '*'
String calcCRC(char* buff, byte buff_len) {
  char c;
  byte i;
  byte start_with = 0;
  byte end_with = 0;
  byte crc = 0;

  for (i = 0; i < buff_len; i++) {
    c = buff[i];
    if (c == '$') start_with = i;
    else if (c == '*') end_with = i;

  }
  if (end_with > start_with) {
    for (i = start_with + 1; i < end_with; i++) {
      crc = crc ^ buff[i];  // XOR every character between '$' and '*'
    }
  } else {
#ifdef DEBUG
    Serial.println("CRC ERROR");
#endif
    return "-1";
  }
  return String(crc, HEX);
}

void forwardMsgToPOZYX() {

#ifdef DEBUG
  Serial.print("Ox");
  Serial.print(pozyx_data.source_id, HEX);
  Serial.print(": ");
  Serial.println(inputString);
#endif

  int length = inputString.length();
  uint8_t buffer[length];
  inputString.getBytes(buffer, length);

  // write the message to the transmit (TX) buffer
  int status = Pozyx.writeTXBufferData(buffer, length);
  // broadcast the contents of the TX buffer
  status = Pozyx.sendTXBufferData(0);

  inputString = "";
  stringComplete = false;
}

void forwardMsgToFC() {
  uint8_t msg_length = 0;
  uint16_t messenger = 0x00;
  delay(1);

  // Let's read out some information about the message (i.e., how many bytes did we receive and who sent the message)
  Pozyx.getLastDataLength(&msg_length);
  Pozyx.getLastNetworkId(&messenger);
  char data[msg_length];

  // read the contents of the receive (RX) buffer, this is the message that was sent to this device
  // TODO: what if msg is greater than pozyx buffer?!
  Pozyx.readRXBufferData((uint8_t *) data, msg_length);

#ifdef DEBUG
  Serial.print("Ox");
  Serial.print(messenger, HEX);
  Serial.print(": ");
  Serial.print(data);
#endif

  // send data over uart to fc
  msp.write(data, msg_length);
}

void forwardNavigation(unsigned long currentTime) {

  t_gps = millis();

  String t = formatTime(currentTime);
  String date = "011219";

  String str = "$"
               + String(ID_NAV) + ","
               + t + ","
               + date + ","
               + pozyx_data.coordinates.x + ","
               + pozyx_data.coordinates.y + ","
               + pozyx_data.coordinates.z + ","
               + "*";
  byte len = str.length() + 1;
  char buff[len];

  // TODO: fix String->Char, Char->String conversions!
  str.toCharArray(buff, len);
  String gps_msg = str + calcCRC(buff, sizeof(buff));

#ifdef PRINT_POSITION
  Serial.println(gps_msg);
#endif
}

void forwardOrientation(unsigned long currentTime) {
  t_mag = millis();

  //example msg: $GPRMC , 161229.487,A,3723.2475,N,12158.3416,W,0.13,309.62,120598, ,*10

  String str = "$"
               + String(ID_MAG) + ","
               + pozyx_data.magnetic.x + ","
               + pozyx_data.magnetic.y + ","
               + pozyx_data.magnetic.z + ","
               + pozyx_data.linear_velocity.x + ","
               + pozyx_data.linear_velocity.y + ","
               + pozyx_data.linear_velocity.z + ","
               + "*";
  byte len = str.length() + 1;
  char buff[len];

  // TODO: fix String->Char, Char->String conversions!
  str.toCharArray(buff, len);
  String mag_msg = str + calcCRC(buff, sizeof(buff));
#ifdef PRINT_ORIENTATION
  Serial.println(mag_msg);
#endif
}

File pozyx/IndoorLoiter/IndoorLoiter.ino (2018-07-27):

#include <Pozyx.h>
#include <Pozyx_definitions.h>

#include <SoftwareSerial.h>
#include <Wire.h>

////////////////// Pozyx Prams //////////////////////////////
//#define CONFIG_TX_GAIN 33.5f
#define CONFIG_TX_GAIN 33.0f

#define NUM_ANCHORS 4
// the network id of the anchors: change these to the network ids of your anchors.
/*uint16_t anchor_id[4] = { 0x601C, // (0,0)
                          0x6020, // x-axis
                          0x6057, // y-axis
                          0x605E};*/

uint16_t anchor_id[4] = { 0x690b, // (0,0)
                          0x6951, // x-axis
                          0x695d, // y-axis
                          0x6e59};

// only required for manual anchor calibration.
// Please change this to the coordinates measured for the anchors
int32_t th = 750;
int32_t anchors_x[NUM_ANCHORS] = {-3638, -3231, 3460, 2081};    // anchor x-coorindates in mm (horizontal)
int32_t anchors_y[NUM_ANCHORS] = {973  , -9997,-1217, -9997};    // anchor y-coordinates in mm (vertical)
int32_t heights[NUM_ANCHORS] =   {-3000+th, -1500+th, -2500+th, -2000+th};    // anchor z-coordinates in mm (1.2m above vehicle's starting altitude)

// RX TX serial for flight controller ex) Pixhawk
// https://github.com/PaulStoffregen/AltSoftSerial
SoftwareSerial fcboardSerial(10, 11); // rx, tx

#define MSG_HEADER          0x01
#define MSGID_BEACON_CONFIG 0x02
#define MSGID_BEACON_DIST   0x03
#define MSGID_POSITION      0x04

// structure for messages uploaded to ardupilot
union beacon_config_msg {
    struct {
        uint8_t beacon_id;
        uint8_t beacon_count;
        int32_t x;
        int32_t y;
        int32_t z;
    } info;
    uint8_t buf[14];
};
union beacon_distance_msg {
    struct {
        uint8_t beacon_id;
        uint32_t distance;
    } info;
    uint8_t buf[5];
};
union vehicle_position_msg {
    struct {
        int32_t x;
        int32_t y;
        int32_t z;
        int16_t position_error;
    } info;
    uint8_t buf[14];
};
////////////////////////////////////////////////

void setup()
{
    Serial.begin(115200);
    fcboardSerial.begin(115200);

    if (Pozyx.begin() == POZYX_FAILURE) {
        Serial.println(("ERR: shield"));
        delay(100);
        abort();
    }

    Serial.println(("V1.0"));

    // clear all previous devices in the device list
    Pozyx.clearDevices();

    // configure beacons
    /*while (!configure_beacons()) {
        delay(1000);
    }*/

    // if the automatic anchor calibration is unsuccessful, try manually setting the anchor coordinates.
    // fot this, you must update the arrays anchors_x, anchors_y and heights above
    // comment out the doAnchorCalibration block and the if-statement above if you are using manual mode
    SetAnchorsManual();

    print_anchor_coordinates();

    Serial.println(("Waiting.."));
    delay(5000);

    Serial.println(("Starting: "));
}

void loop()
{
    static uint32_t loop_start = 0;
    static uint8_t stage = 0;   // 0 = initialisation, 1 = normal flight
    static uint16_t beacon_sent_count = 0;
    static uint32_t beacon_sent_time = 0;

    // initialise start time
    if (loop_start == 0) {
        loop_start = millis();
    }

    // advance to normal flight stage after 1min
    if (stage == 0) {
        uint32_t time_diff =  (millis() - loop_start);
        if (time_diff > 60000) {
            stage = 1;
            Serial.println("Stage1");
        }
    }

    // slow down counter
    static uint8_t counter = 0;
    counter++;
    if (counter >= 20) {
        counter = 0;
    }

    // during stage 0 (init) send position and beacon config as quickly as possible
    // during stage 1 send about every 2 seconds
    if (stage == 0 || counter == 0) {
        send_beacon_config();
        get_position();
        if (beacon_sent_count > 0 && beacon_sent_time != 0) {
            uint32_t time_diff = millis() - beacon_sent_time;
            float hz = (float)beacon_sent_count / (time_diff / 1000.0f);
            Serial.print("Beacon hz:");
            Serial.println(hz);
        }
        beacon_sent_count = 0;
        beacon_sent_time = millis();
    }

    // send beacon distances
    get_ranges();
    beacon_sent_count++;
}

uint32_t time_start_ms;
void timer_start()
{
    time_start_ms = millis();
}
void timer_end()
{
    uint32_t time_diff = millis() - time_start_ms;
    Serial.print("ms:");
    Serial.println(time_diff);
}

void print_comma()
{  
    Serial.print(",");
}

void print_tab()
{  
    Serial.print("\t");
}

// set a tag or anchor's gain
//   set tag_id to zero to set local device's gain
//   returns true on success
bool set_device_gain(uint16_t dev_id, float gain)
{
    float tx_power = -1;

    // get/set transmit power of tag
    bool gain_ok = false;
    uint8_t retry = 0;
    while (!gain_ok && retry < 5) {
        if (Pozyx.getTxPower(&tx_power, dev_id) == POZYX_SUCCESS) {
            if (tx_power != gain) {
                Pozyx.setTxPower(CONFIG_TX_GAIN, dev_id);
            } else {
                gain_ok = true;
            }
        }
        retry++;
    }

    // display final gain
    Serial.print("Dev ");
    Serial.print(dev_id, HEX);
    Serial.print(" gain ");
    if (tx_power > 0) {
        Serial.print(tx_power);
    } else {
        Serial.print("unknown");
    }
    Serial.print(" (retry ");
    Serial.print(retry);
    Serial.print(")");
    Serial.println();

    return gain_ok;
}

// performs repeated calls to get reliable distance between devices
bool get_remote_range(uint16_t dev1, uint16_t dev2, int32_t& range)
{
    // set distances between tags
    uint32_t range_tot = 0;
    uint16_t count = 0;
    device_range_t dev_range;
    for (uint8_t i=0; i <= 10; i++) {
        // origin to 1st
        if (Pozyx.doRemoteRanging(dev1, dev2, &dev_range) == POZYX_SUCCESS) {
            range_tot += dev_range.distance;
            count++;
        }
        if (Pozyx.doRemoteRanging(dev2, dev1, &dev_range) == POZYX_SUCCESS) {
            range_tot += dev_range.distance;
            count++;
        }
    }
    // success if at least 5 successful ranges were retrieved
    if (count > 5) {
        range = range_tot / count;
        return true;
    }
    return false;
}

void print_failed_to_range(uint16_t dev1, uint16_t dev2)
{  
    Serial.print("ranging fail ");
    Serial.print(dev1,HEX);
    Serial.print(" to ");
    Serial.println(dev2,HEX);
}

void set_beacon_position(uint8_t index, int32_t x_mm, int32_t y_mm, int32_t z_mm)
{
    anchors_x[index] = x_mm;
    anchors_y[index] = y_mm;
    heights[index] = z_mm;
}
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

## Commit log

2018-07-27 init folder structure and added win drivers and pozyx arduino sketch
2018-08-03 added inav-2.0.0 with modified target.h
    [generator_config.txt]
2018-08-08 added docs for gps setup, inserted //TODO where gps messages are probably beeing read
2018-08-17 added simple unit test in build chain
2018-08-24 added 3d model for receiver base
    [receiver_base.stl]
2018-08-31 added new model for foot
    [new_foot.stl, new_foot_2.stl, new_foot_3.stl]
2018-09-07 Added frame measurement
2018-09-28 added battery holder
    [bat_holder.stl, bat_holder_v2.stl, bat_holder_v3.stl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]
2018-10-05 updated battery info
2018-10-05 added nmea related info and arduino test sketch
2018-10-05 added naza decoder library and first sketch of nav/mag simulator - Naza gps module uses UART for both, mag and nav communication
2018-11-22 cleanup unnecessary arduino sketches
2018-11-22 added pozyx arduino sketch
2018-11-22 stm32 documentation and fc backup
2018-11-22 cleanup arduino
2018-12-13 arduino sketch update
2019-01-24 arduino pozyx sketch cleanup
2019-01-24 arduino pozyx sketch fix tag id
    [pozyx.ino]
2019-01-31 3d print object - pozyx holder plate
    [Pozyx_holder.skp, Pozyx_holder.stl]
2019-02-01 Arduino Nano now in loop until pozyx is initialized
    No need to reboot nano when pozyx not connected
    [pozyx.ino]
2019-02-20 gui fix, save button was not visible
2019-02-20 added new button to pozyx to connect to serial
2019-02-20 first try for serial communicatoin with arduino hello world
2019-02-20 added einkaufliste
    [20190202-einkaufliste.ods]
2019-02-20 updated pozyx holder
    [Pozyx_holder.skp, Pozyx_holder.stl, pozyx_holder.stl]
2019-02-20 changes on einkaufsliste
    [20190202-einkaufliste.ods]
2019-02-28 Sendet nun an Alle die Nachrichten und empfaengt beliebig lange Nachrichten. Nachricht muss momentan noch 1 extra char am Ende haben
2019-02-28 arduino now simulates groundCourse heading data
2019-03-05 implemented serial connect on default connect button
2019-03-05 remove test button serialConnect
2019-03-07 add communication_Onword data with return methodes for the devicelist and the taglist. added send_test_message receiver attribute
2019-04-05 added msp msg forwarding to pozyx arduino, also some cleanup. TODO: test waitforflag without delay, test for big buffer messages >24bytes, use softserial port for msp msgs only
2019-04-10 implemented softserial for msp messages on nano
    nano now sends gps + mag to fc uart1 and forwards msp pozyx messages to uart3
2019-04-10 fixed driver issue (DFU mode)
    minor python script changes
2019-04-11 moved to py script button
2019-04-11 Fix pozyx driver issue for ubuntu
    fixed ubuntu driver issue, where id is lowercase
2019-04-12 mag is now supported in inav, fixed positioning
    fixed pozyx positioning, added mag x/y/z values to mag_msg
    [MSPHelper.js, pozyx.ino]
2019-04-17 3d file for receiver and arduino base
    [base_ardu_rec.stl, dev_tag.obj, plate_ardu_rec.FCStd]
2019-04-17 arduino message optimisation
    removed unnecessary time, altitude
2019-05-09 added TODOs regarding gps precision and failure
    [MSPHelper.js]
2019-05-09 updated nav & mag msg (gps,velNED,mag)
    TODO check if parsed correctly and all values are set inside fc
    [pozyx.ino]
2019-05-09 debug msgs and quick fix that should be removed later on
    remove me later on
    [MSPHelper.js]
2019-05-10 TODO implement msg forwarding for position error
    [pozyx.ino]
2019-05-10 removed millis from time msg and shortened statemachine
2019-05-19 cranked up mag & gps task period on fc and fixeed num of satelites
    [pozyx.ino]
2019-05-22 removed MSP_RAW_GPS_POZYX and implemented anchor positions in gui. TODO scale correctly
    [MSPHelper.js, fc.js]
2019-05-27 transformation of velNED from body frame to earth frame
2019-05-27 transformation of velNED from body frame to earth frame TODO test flight
2019-05-29 added tag dropdown again
    !!WARNING!!
    remote_id = none not working,
    only 1 switch possible
2019-05-29 arduino sends messages to fc only when values are new
2019-08-09 added circuit diagram

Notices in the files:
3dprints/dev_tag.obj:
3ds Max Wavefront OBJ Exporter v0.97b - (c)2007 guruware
